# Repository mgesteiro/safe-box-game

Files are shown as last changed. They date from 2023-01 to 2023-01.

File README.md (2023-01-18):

# Safe BOX GAME puzzle-box

This is a **funny puzzle-box** game in which you have to try to guess -using the lights- the correct four digit code to open the safe box.

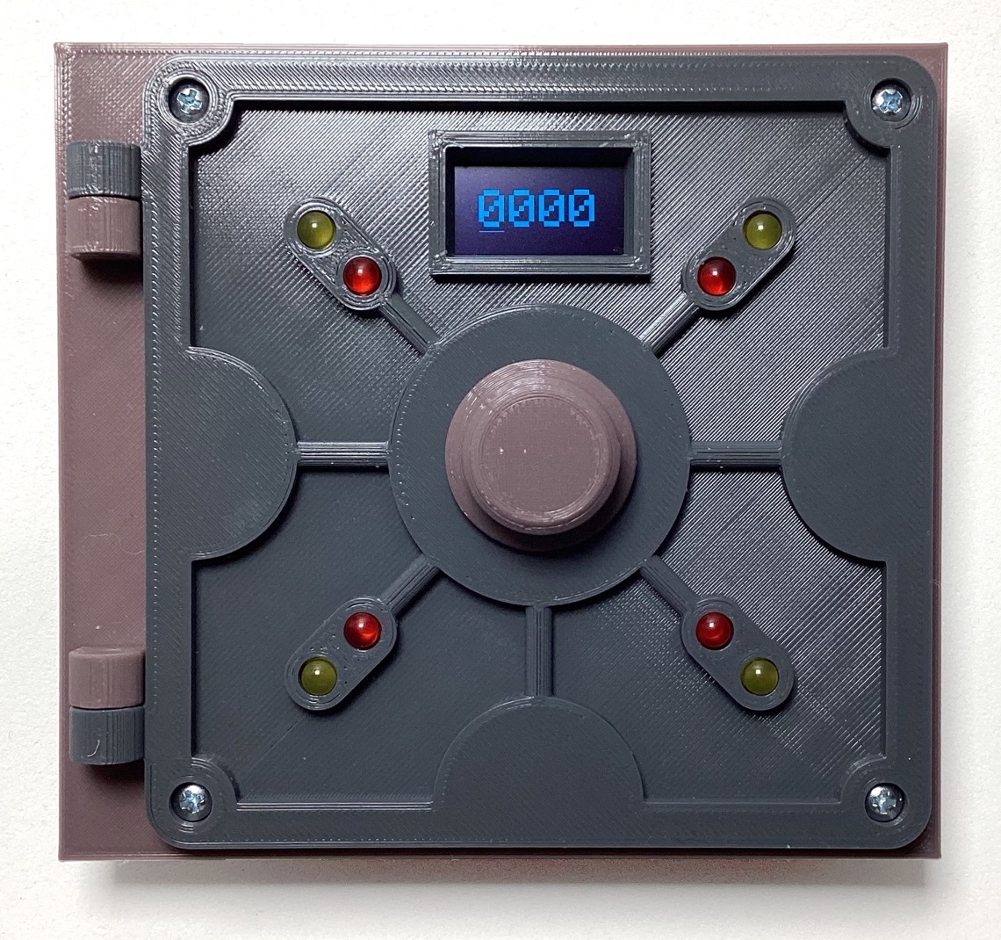
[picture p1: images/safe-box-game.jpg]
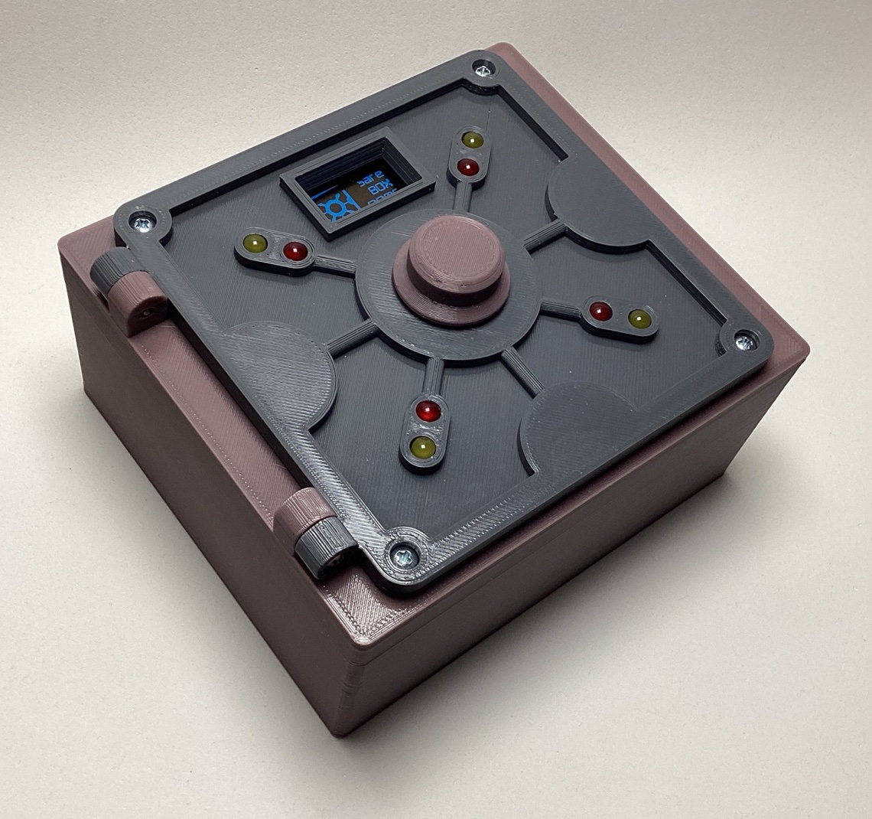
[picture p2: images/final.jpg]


This puzzle-box game was inspired by and based on [this project](https://www.the-diy-life.com/crack-the-code-game-built-into-a-diy-safe-puzzle-box/), making it **more compact** (it's all self-contained now), **3D printed** (instead of laser cut) and **rechargable**.

Any sugestion? Please, **contact me**.

## USAGE

The box is unlocked when it's off, so you can open the door if you want. These are the steps:

* Turn-on the system pressing the switch in the back of the door (inside the box when closed): you'll see a welcome screen.
* After that, a message appears asking you to press the knob to lock the door: close the door and press it.
* Now you have a four digit code in the screen: rotate the know to change the number, and press it to go to the next digit.
* When you press the knob in the last digit, the safe checks the combination: if it is right, the door will unlock and you'll have won; if not, it will tell you so and the *lights* will indicate how many digits were correct and how many were in the correct position.
* Repeat until you get it!

**NOTE:** there is a blinking light (every two seconds) that has NO meaning. It's just an *I'm alive* signal.

## WHY and HOW

The original project was **very very** appealing, but had **two big drawbacks** for me:

* I don't have a laser cutter (but yes a 3D-printer), and
* The control and electronic components were **too spread** (part in the door, part in the back).

Based on my experience in previous projects, I was convinced that it could be done in a much more compact form, using also a rechargable system and improving a little bit the UX (that was excellent to begin with).

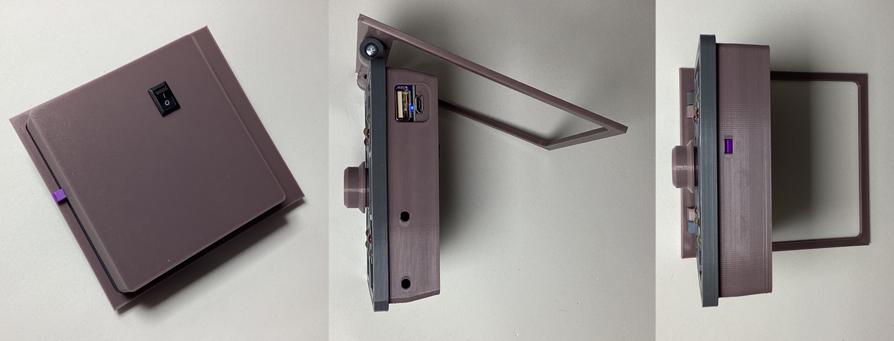
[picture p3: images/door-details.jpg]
door-details

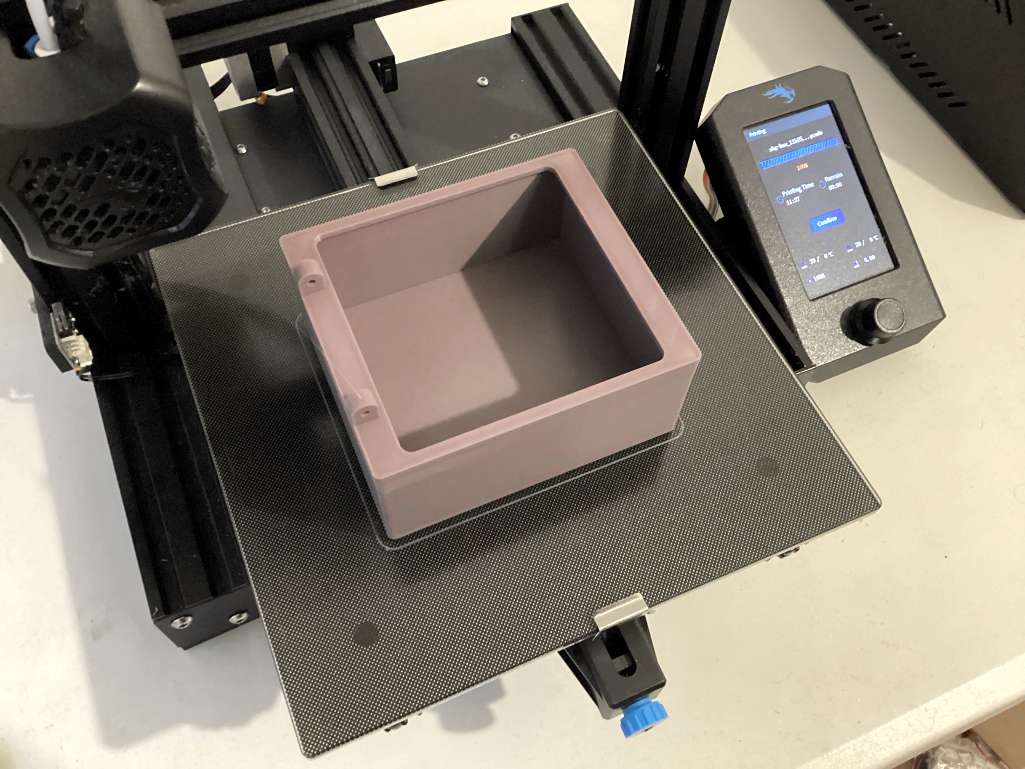
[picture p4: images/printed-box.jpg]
printed-box


And here it is the result, after a little bit more effort than I anticipated... 😅

## 3D

All the **3D parts** (available in the [`3D`](3D) folder) were created using the open-source and free software [FreeCAD](https://www.freecad.org). If you want, for example, a bigger box, go ahead and edit the 3D file to do so. In the [`STLs`](3D/STLs) subfolder reside all the STL files ready to be 3D printed, with **no supports** required at all: it's a very easy print.

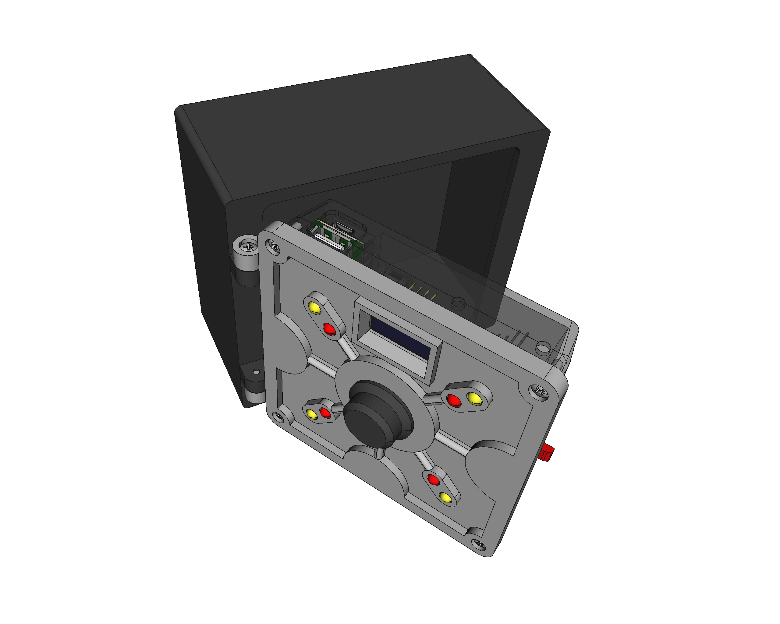
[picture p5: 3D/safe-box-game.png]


There were some interesting **design challenges**, like how to make all the parts ***no-support-required*** 3D-printable, that led to interesting choices that I wouldn't have done other way: the (***good looking***) screws holding the door together are accesible from the outside, and, from a *security perspective*, that would've been disastrous... if this was a *real* safe-box. It actually became a ***handy feature***: if anything anomalous/unexpected happens (battery depletion?) and you can't open the box, you have always the option to disassemble it unscrewing those four screws 👌

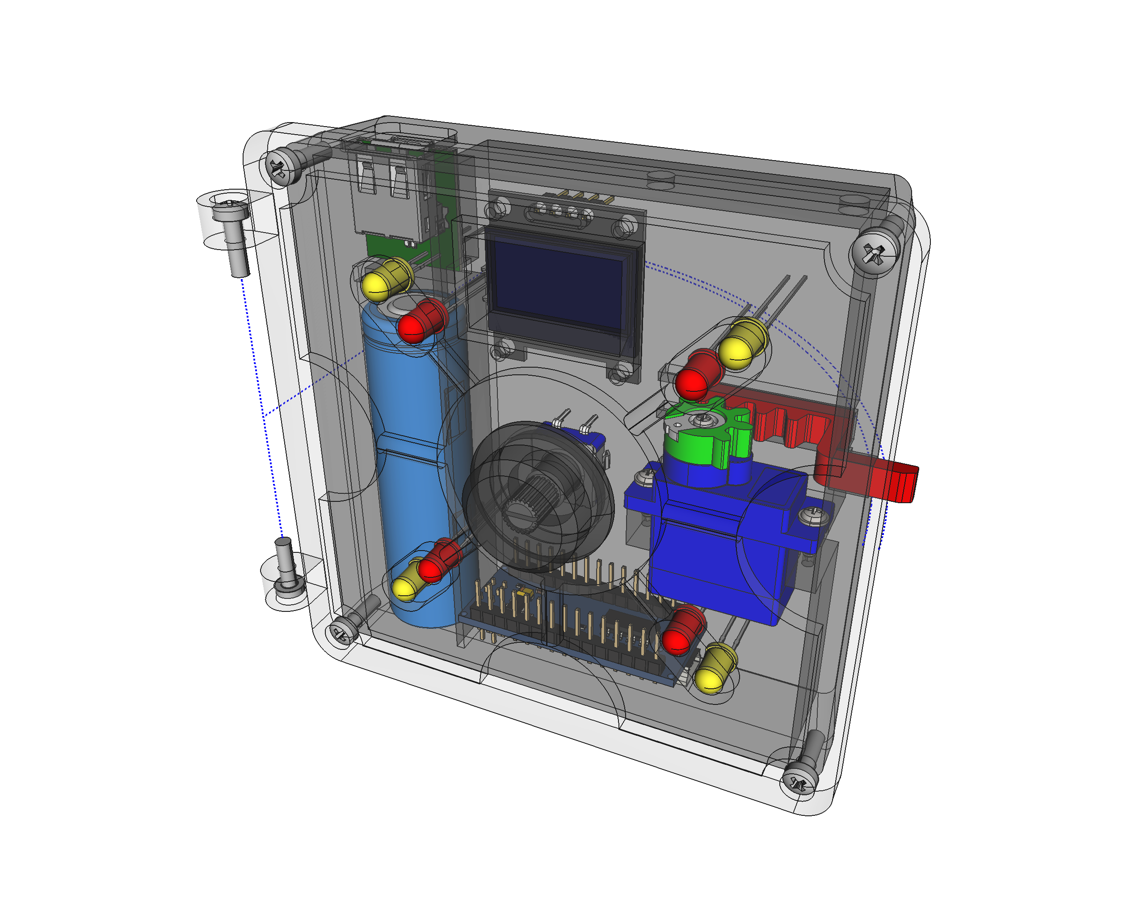
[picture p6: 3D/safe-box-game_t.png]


Did you notice the blue dashed lines? Yep, they were added after realizing that the door was going to be **THICK** and that I needed to change the design to provide rotation clearance without making it even bigger or make a too lousy frame (compact, remember?). After some back and forth between the door, the hinges and the frame, everything  ended up really well. 

This is also the first time I've worked with [*gears & racks*](3D/servo-gearandrack), but was a nice opportunity to make the locking mechanism much more nicer than just a *big rotating contraption*, and contributed to make everything more compact. I had also to \[re\]create some parts, like the [SDD1306 oled display](https://github.com/mgesteiro/FreeCAD-models/tree/master/SSD1306_128x64), because the available models didn't match what I had at hand.

At the end, the door looks like a *real* safe-box door, with all its thickness and shape and weight ... **I ❤️ it!**.

## CONNECTIONS

This is the schematic of the system, created using the open-source software [Fritzing](https://fritzing.org) and available in the [`connections`](connections) folder.

connections

In the original project, the servo was connected directly to the Arduino 5V output, which is generally not recommended (even for the small SG90 micro-servo**). As I opted to power everything with a 5V powerbank-DIY kit, the servo can be powered directly (althoug a capacitor in parallel is always a good idea...), making the whole device also **rechargable**.

** as it may demand quite a lot of current that the Arduino may not be able to provide and get *swamped* in the process, resetting itself.

In the physical world it was a little more difficult than I wanted, but with patience, care and some *creativity* and *dexterity*, it ended up nicely:

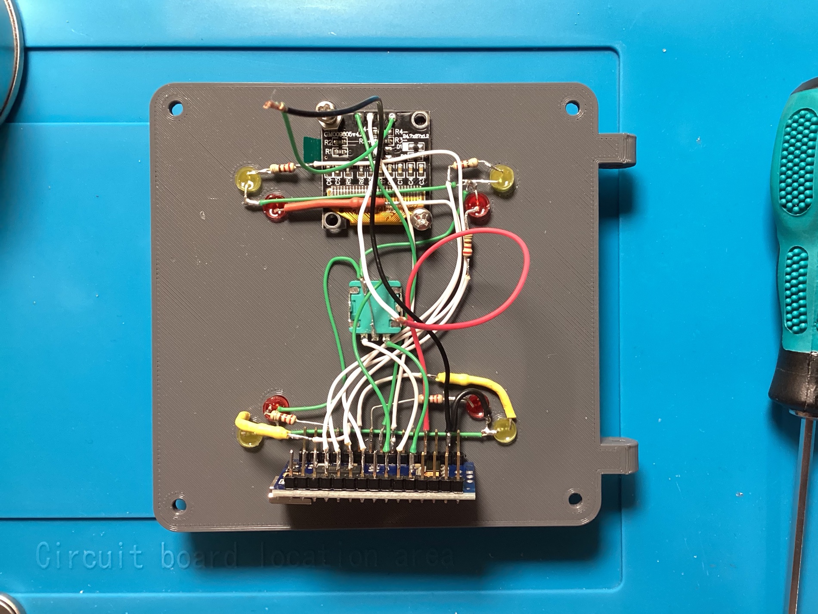
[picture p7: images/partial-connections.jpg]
partial-connections


The most difficult part were the LEDs to the right, that had to go flat because they are under the rechargable system with very little space. The servo also played an important role in *limiting* the available space. The [3D model](#3d) was very useful to navigate all these problems beforehand and during the assembly.

## CODE

The puzzle-box is powered by an **Arduino Nano** which can be programmed with the [Arduino IDE](https://www.arduino.cc/en/software). The code itself is available in the [`code/sbg`](code/sbg) folder:

* It solves a bug in the original project's code, where there were no **9**'s in the digits, due to an incorrect use of the [`random()`](https://www.arduino.cc/reference/en/language/functions/random-numbers/random/) function.
* Nice cursor to indicate which digit is being manipulated.
* It comes with and *adhoc* library (***RotEnLib***) to manage the rotary encoder (with momentary push button) and make the code simpler while having nice features like *debouncing* and *round-robin* hidden away.
* It has some configuration parameters at the beginning (`sbg.ino`) that can be adjusted to your needs.
* There is some code to avoid the powerbank auto-shuting-down function (that's why the LEDs blink!).
* And a nice *splash screen* (see [`code/logo`](code/logo)).



## REFERENCES

* Crack-the-Box project by Michael Klemets from the The DIY Life: [www.the-diy-life.com/crack-the-code-game-built-into-a-diy-safe-puzzle-box/](https://www.the-diy-life.com/crack-the-code-game-built-into-a-diy-safe-puzzle-box/)
* Arduino `random()` function: [www.arduino.cc/reference/en/language/functions/random-numbers/random/](https://www.arduino.cc/reference/en/language/functions/random-numbers/random/)
* My FreeCAD 3D models repository: [github.com/mgesteiro/FreeCAD-models](https://github.com/mgesteiro/FreeCAD-models)
* My Fritzing parts repository: [github.com/mgesteiro/fritzing-parts](https://github.com/mgesteiro/fritzing-parts)
* **FreeCAD** 3D CAD modelling software: [www.freecad.org](https://www.freecad.org)
* **Fritzing** schematics and PCB modelling software: [fritzing.org](https://fritzing.org)

## LICENSE

This work is licensed under the [GNU General Public License v3.0](LICENSE-GPLV30). All media and data files that are not source code are licensed under the [Creative Commons Attribution 4.0 BY-SA license](LICENSE-CCBYSA40).

More information about licenses in [Opensource licenses](https://opensource.org/licenses/) and [Creative Commons licenses](https://creativecommons.org/licenses/).

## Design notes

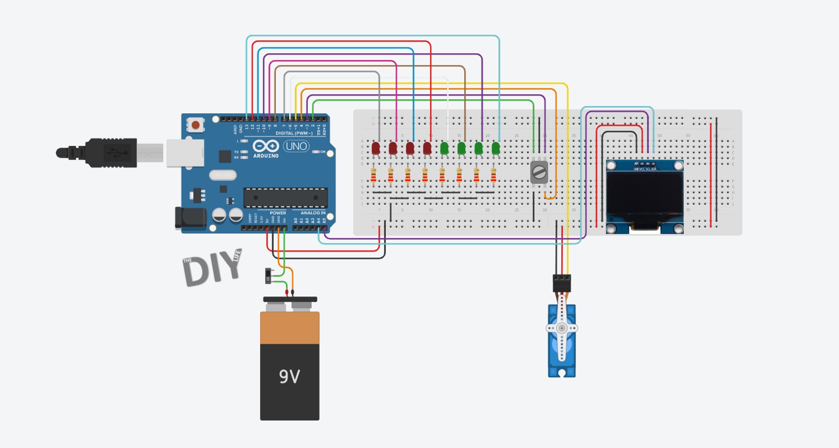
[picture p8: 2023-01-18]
docs/Crack-The-Code-Schematic.jpg

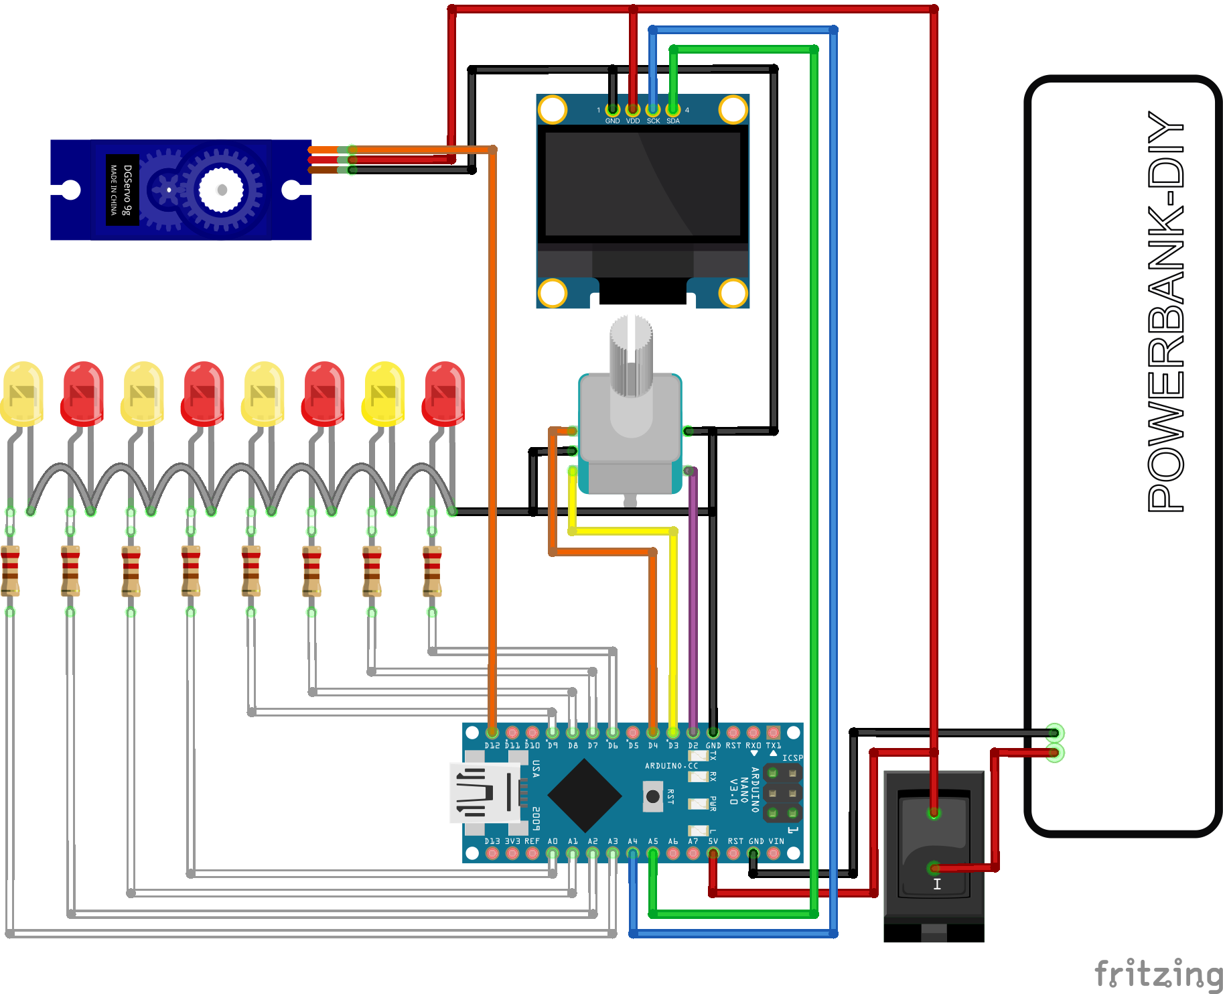
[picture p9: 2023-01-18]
connections/connections_bb.png

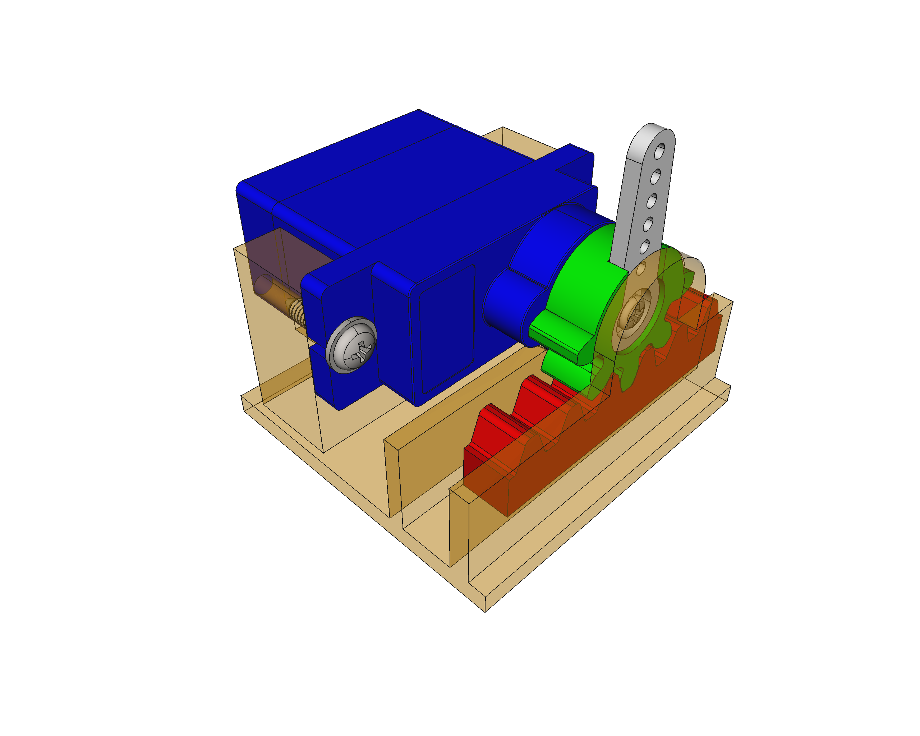
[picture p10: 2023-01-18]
3D/servo-gearandrack/servo-gearandrack.png

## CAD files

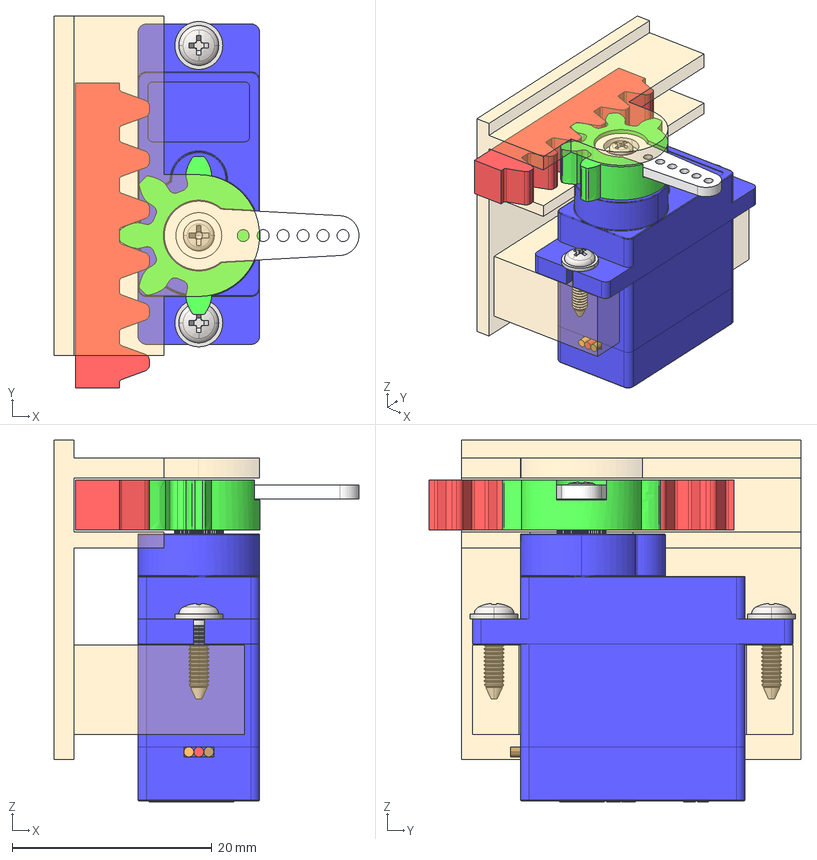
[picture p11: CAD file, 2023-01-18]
3D/servo-gearandrack/servo-gearandrack.FCStd
30.6 x 37.3 x 36.2 mm
Body-gear
Body-rack
Body-servo-support
arm1
screw-shaft
screw1
screw2
body-screws x 2
w1 x 2
shaft x 2
w3 x 2
w2 x 2

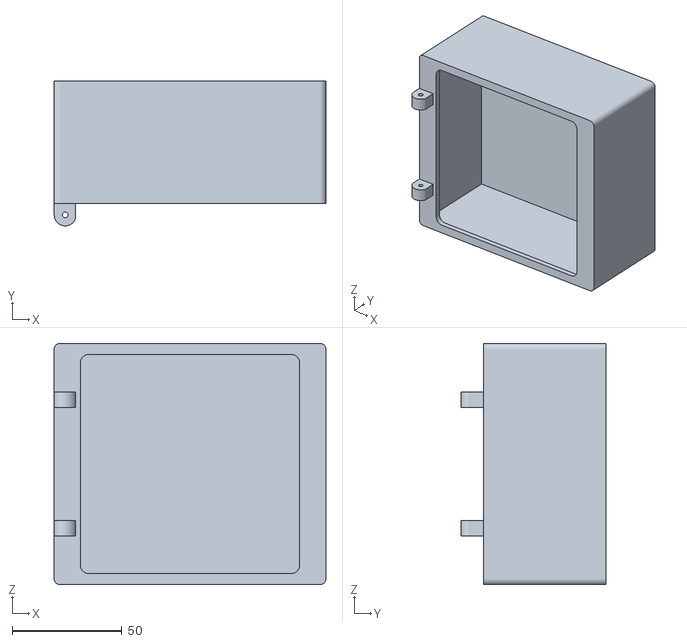
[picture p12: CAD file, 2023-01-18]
3D/STLs/sbg-box.stl
124.0 x 66.0 x 110.0

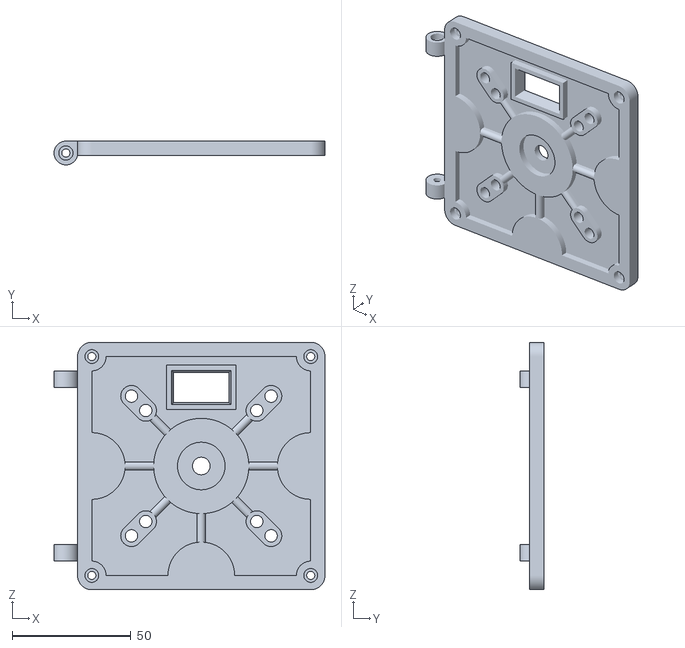
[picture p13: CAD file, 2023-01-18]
3D/STLs/sbg-door.stl
113.9 x 10.00 x 104.0

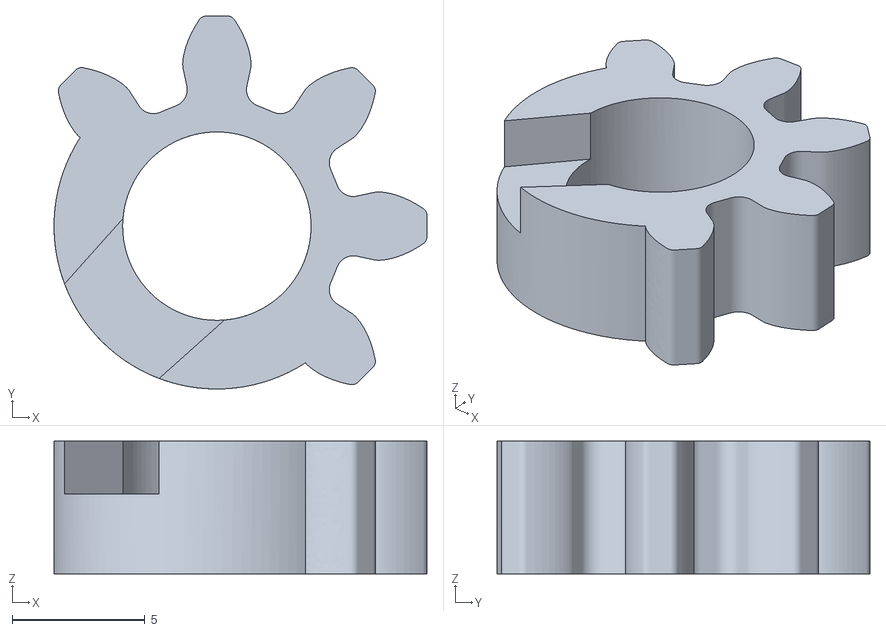
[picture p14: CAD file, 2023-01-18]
3D/STLs/sbg-gear.stl
14.1 x 14.1 x 5.00

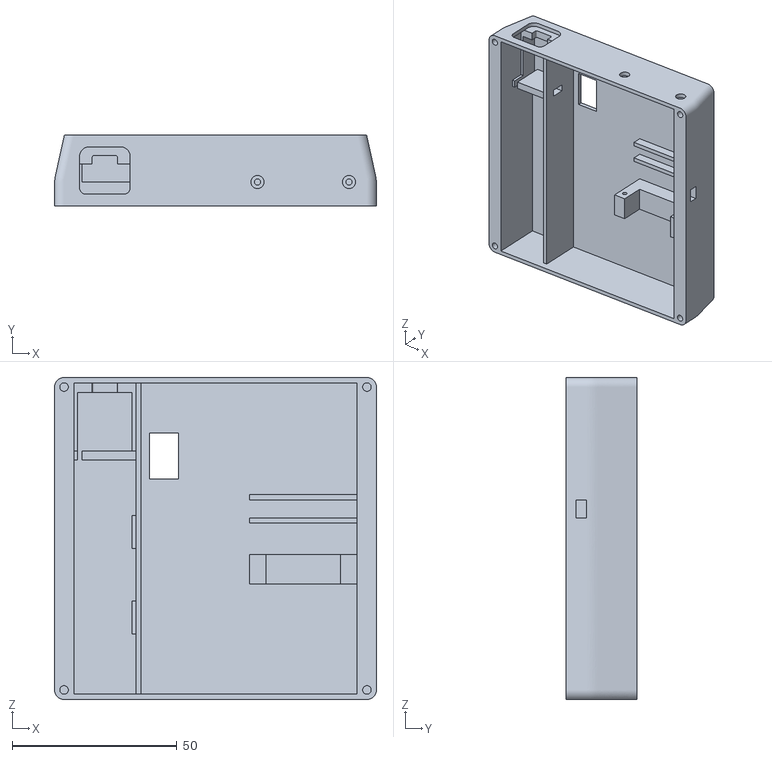
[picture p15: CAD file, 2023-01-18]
3D/STLs/sbg-electronic-box.stl
97.8 x 21.6 x 97.8

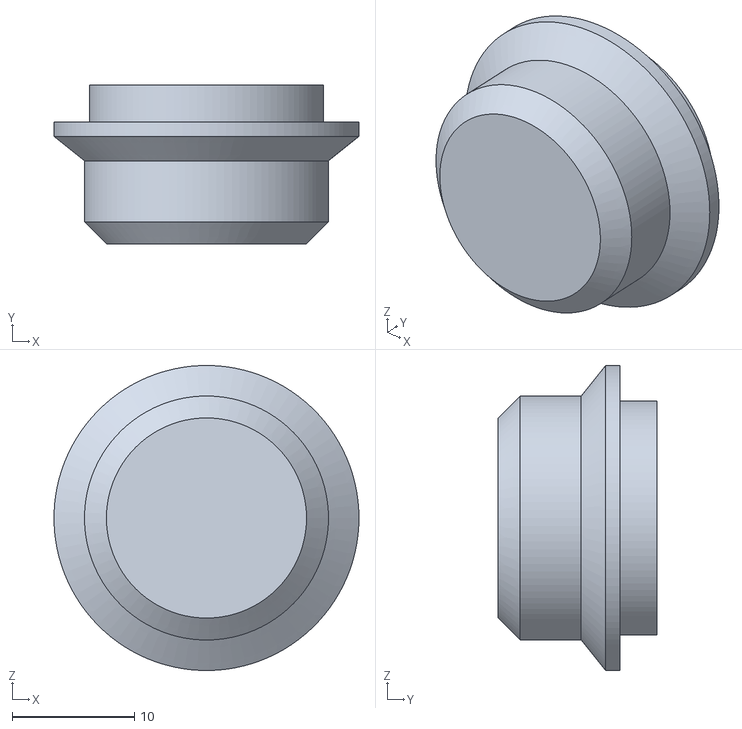
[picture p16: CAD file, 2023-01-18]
3D/STLs/sbg-knob.stl
25.0 x 13.0 x 25.0

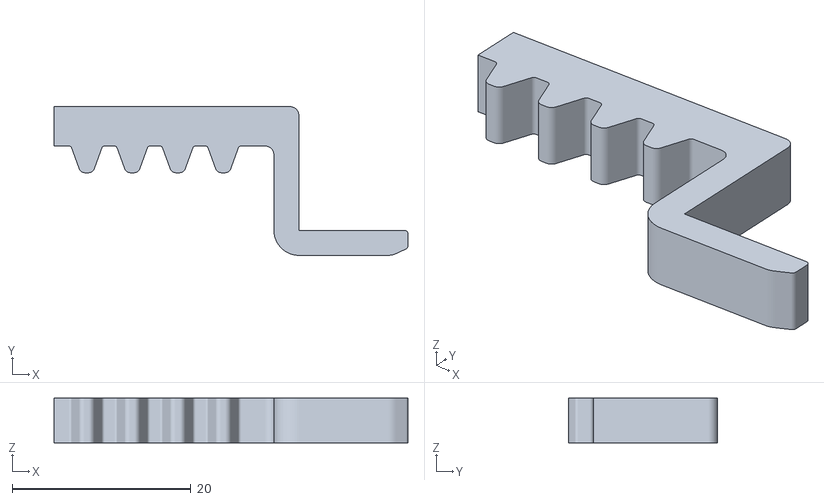
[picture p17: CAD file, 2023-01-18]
3D/STLs/sbg-rack-lock.stl
39.6 x 16.6 x 5.00

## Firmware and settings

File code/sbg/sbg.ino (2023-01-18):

/**
 * Safe BOX GAME firmware.
 *
 * @author mgesteiro
 * @version 1.0.0
 * @date 20230115
 * @copyright OpenSource, LICENSE GPLv3 and CCSABY40
 *
 * Libraries required: "Servo" and "Adafruit_SSD1306" (and dependencies)
 */

#define VERSION "1.0.0"

// CONFIGURATION
#define REL_PINA 2
#define REL_PINB 3
#define REL_BTN 5
#define SCREEN_ADDRESS 0x3C
#define SERVO_PIN 12
#define SERVO_UNLOCKED 110
#define SERVO_LOCKED 55
#define SHOW_RESULTS_IN_SCREEN false

#include "RotEnLib.h"  // rotary encoder library
#include <Adafruit_SSD1306.h>
#include "SBGlogo.h"  // startup screen
#include <Servo.h>

RELEncoder encoder = RELEncoder(REL_PINA, REL_PINB, REL_BTN, 0, 9, true); // pinA, pinB, btn, min, max, circular
Adafruit_SSD1306 display(128, 64, &Wire, -1);
Servo lockServo;

const uint8_t correctPositionPins[] = {7, 8, A2, A1};
const uint8_t correctNumberPins[]   = {6, 9, A3, A0};
uint8_t code[4], guess[4];
uint8_t currentDigit = 0;

uint32_t tactivity = 0;
uint8_t LEDstate = 0;

/**
 *******************************************************************************
 *   S E T U P   &   L O O P
 */

void setup()
{
  Serial.begin(9600);
  Serial.print("Safe BOX GAME v");
  Serial.println(VERSION);
  // LEDs
  initLEDs();
  // Encoder button callback
  encoder.setButtonOnPressCB(onButtonPressed);
  encoder.init();
  // Display
  if (!display.begin(SSD1306_SWITCHCAPVCC, SCREEN_ADDRESS))
    Serial.println(F("SSD1306 allocation failed"));
  display.setTextColor(SSD1306_WHITE);
  // Servo
  lockServo.attach(SERVO_PIN);
  lockServo.write(SERVO_UNLOCKED);  // unlock the safe
  // Seed PRNG
  randomSeed(analogRead(A7));  // noise from A7 (not connected = floating)
  // Do intro
  doSplash();
  introLEDs();
  // Do start
  doStart();
}  // setup()

void loop()
{
  // avoids power-bank shutting down
  checkStandBy();

  // update encoder status
  encoder.loop();

  // get encoder position
  uint8_t position = encoder.getPosition();

  // redraw output if necessary
  if (position != guess[currentDigit])
  {
    guess[currentDigit] = position;
    updateDisplay(guess, currentDigit);
  }

  // the rest of the logic is done at the
  // encoder's onButtonPressed() callback
  // function where the "clicks" are processed

}  // loop()


/**
 *******************************************************************************
 *   S U P P O R T   F U N C T I O N S
 */

 void initLEDs()
{
  for (uint8_t i = 0; i < 4; i ++)
  {
    pinMode(correctPositionPins[i], OUTPUT);
    pinMode(correctNumberPins[i], OUTPUT);
  }
}

/**
 * Turn on/off each LED individually in bulk.
 *
 * @param state 1 bit per LED. Low nibble for "correct position" LEDs and
 *              high nibble for "correct number" LEDs.
 */
void turnLEDs(uint8_t state)
{
  LEDstate = state;  // save for standby check
  for (uint8_t i = 0; i < 4; i ++) digitalWrite(correctPositionPins[i], bitRead(state, i));
  for (uint8_t i = 4; i < 8; i ++) digitalWrite(correctNumberPins[i-4], bitRead(state, i));
}

/**
 * Show splash screen
 */
void doSplash()
{
  display.clearDisplay();
  display.drawBitmap(0, 0, logo_data, 128, 64, 1);  // put logo
  display.display();  // show logo
  delay(1000);
}

/**
 * LEDs animation.
 */
void introLEDs()
{
  // nice crack the code original animation
  uint8_t Anim[][2] =
  {
    {B00001111, 30},  // state, delay (in 10ms chunks)
    {B11110000, 30},
    {B00001111, 30},
    {B11110000, 30},
    {B11111111, 130},
  };
  for (uint8_t i = 0; i < sizeof(Anim)/2; i ++)
  {
    turnLEDs(Anim[i][0]);
    delay(Anim[i][1]*10);
  }
  turnLEDs(0);
}  // introLEDs()

/**
 * Generate a new code and clear current guess.
 */
void doCodes(bool show)
{
  for (uint8_t i = 0; i < 4; i ++)
  {
    code[i] = random(0,10);  // values from 0 to 9
    guess[i] = 0;
  } 
  // show code
  if (!show) return;
  Serial.print("New code: ");
  for (uint8_t i = 0; i < 4; i ++) Serial.print(code[i]);
  Serial.println();
}  // doCodes()

/**
 * Cycles through the "open", "wait for click", and "closed" states for
 * the lock. This is done this way because it is always what happens:
 * during the start and after a win.
 */
void doLock()
{
  // first: unlock and show message to lock
  lockServo.write(SERVO_UNLOCKED);  // unlock the safe
  display.clearDisplay();
  //display.invertDisplay(true);
  display.setTextSize(1);
  display.setCursor(30,18);
  display.print(F("pulsa para"));
  display.setTextSize(2);
  display.setCursor(30,30); 
  display.print(F("CERRAR"));
  display.display();
  // second: wait for user input
  waitForClick(0);
  // finally: lock and show the notification for 2 secs.
  lockServo.write(SERVO_LOCKED);  // lock the safe  
  display.clearDisplay();
  display.setTextSize(2);
  display.setCursor(23,25);
  display.print(F("CERRADO"));
  display.display();
  delay(2000);
  //display.invertDisplay(false);
}  // doLock()

/**
 * Shows current guess-code and a cursor under the current digit being manipulated.
 *
 * @param guess guess code introduced by the user
 * @param digitpos position of the digit currently being updated
 */
void updateDisplay(uint8_t guess[], uint8_t digitpos)
{
  String text = "";
  for (uint8_t i = 0; i < 4; i++) text += guess[i];  // code[] to String
  display.setTextSize(4);
  display.clearDisplay();
  // default font size 5x7 (pixels) + 1 pixel separation between characters
  // (SCREEN_WIDTH - CHARACTER_WIDTH * PIXEL_MULTIPLIER * NUMBER_OF_DIGITS - (NUMBER_OF_DIGITS - 1) * PIXEL_MULTIPLIER) / 2
  // (128 - 5 * 4 * 4 - (4 - 1) * 4 ) / 2 = 18 <-- X
  // (SCREEN_HEIGHT - CHARACTER_HEIGHT * PIXEL_MULTIPLIER) / 2
  // ( 64 - 7 * 4 ) / 2 = 18 <-- Y
  display.setCursor(18, 16);  // 16 instead of 18 -> some room for under-cursor
  display.println(text);
  display.drawRect(18 + (digitpos * 24), 47, 20, 3, SSD1306_WHITE);  // under-cursor
  display.display();   
}  // updateDisplay()

/**
 * Shows the valid positions/numbers in the screen.
 *
 * @param validpos number of digits in valid position
 * @param validnum number of valid digits
 */
void showCheckResults(uint8_t validpos, uint8_t validnum)
{ 
  // LEDs
  // lo - positions, hi - numbers
  uint8_t state = B00000000;
  uint8_t mask = B00000001;
  for (uint8_t i = 0; i < validpos; i ++)
  {
    state |= mask;
    mask <<= 1;
  }
  mask = B00010000;
  for (uint8_t i = 0; i < validnum; i ++)
  {
    state |= mask;
    mask <<= 1;
  }
  turnLEDs(state);
  // Display
  display.clearDisplay();
  display.setTextSize(2);
  #if SHOW_RESULTS_IN_SCREEN
  // (128 - 6 * 5 * 2 - 5 * 2 ) / 2 = 29
  // (64 - 2 * 7 * 2 - 1 * 2 ) / 2  = 17
  String text = "NUM: ";
  text += validnum;
  display.setCursor(29, 17);
  display.print(text);
  text = "POS: ";
  text += validpos;
  display.setCursor(29, 33);
  display.print(text);
  #else
  display.setCursor(5, 25);
  display.print("INCORRECTO");
  #endif
  display.display();
}  // showCheckResults()

/**
 * Initialization routine: new code and reset parameters.
 */
void doStart()
{
  doLock();  // unlock, wait for click, lock
  doCodes(true);  // generate new code, clear guess
  currentDigit = 0;  // reset
  encoder.setPosition(guess[currentDigit]);  // reset
  updateDisplay(guess, currentDigit);  // show initial status
}

void doWin()
{
  display.clearDisplay();
  display.setTextSize(2);
  display.setCursor(5, 25);
  display.print("CONSEGUIDO");
  display.display();
  lockServo.write(SERVO_UNLOCKED); // before intro
  introLEDs();
}

/**
 * Callback function to attend the encoder "OnPressed" event
 *
 * @param encoder which encoder sends the event
 * @param when moment in which occurred
 */
void onButtonPressed(RELEncoder& encoder, unsigned long when)
{
  currentDigit ++;  // change to next digit
  if (currentDigit > 3)  // was it the last digit?
  {
    // check provided code
    uint8_t copy[4]; // local copy of code for manipulation
    memcpy(copy, code, 4);
    // checking positions/numbers
    uint8_t validpos = 0, validnum = 0;
    for (uint8_t i = 0; i < 4; i++)
    {
      // valid position
      if (guess[i] == code[i]) validpos ++;
      // valid number
      for (uint8_t j = 0; j < 4; j++)
        if (guess[i] == copy[j]) {
          validnum ++;
          copy[j] = -1; // mark as used
          break; // no more checking
        }
    }
    // checking victory
    if (validpos == 4)
    {
      doWin();  // shows message
      doSplash();  // splash screen
      waitForClick(0);  // user must click
      doStart(); // start-up procedure
      return;
    }
    // show checking results
    showCheckResults(validpos, validnum);
    waitForClick(2000);  // 2 secs. maximum
    turnLEDs(0);
    // go to the beginning
    currentDigit = 0;
  }
  // update
  encoder.setPosition(guess[currentDigit]);
  updateDisplay(guess, currentDigit);

} // onButtonPressed()

/**
 * Checks that there is at least a minimum power consumption,
 * to avoid the power-bank shutting off.
 */
void checkStandBy()
{
  uint32_t tnow = millis();
  if (tnow - tactivity > 2000)
  {
    if (! LEDstate)
    {
      turnLEDs(B01000100 << random(0,2)  );  // turn-on a random pair of LEDs
      delay(5);  // for 5 milliseconds
      turnLEDs(0);
      tactivity = tnow; 
    }
  }
}

/**
 * Waits until the user clicks or the provided milliseconds pass.
 *
 * @param delay max time to wait, in milliseconds. Infinite if value is 0.
 */
void waitForClick(uint32_t tdelay)
{
  if (tdelay == 0) tdelay = 0xffffffff;
  delay(150);  // give time for button to be released
  uint32_t tnow = millis();
  while ( 
    (digitalRead(REL_BTN) == HIGH)
    && (millis() - tnow < tdelay)
  ) checkStandBy();
}

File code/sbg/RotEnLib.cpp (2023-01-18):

// RotEnLib
// --------
// author: mgesteiro
// date: 20211205

#include "RotEnLib.h"
#include "Arduino.h"

#define BTNDEBOUNCETIME 10
#define ENCDEBOUNCETIME 4
#define LONGPRESSTIME 800

// constructor
RELEncoder::RELEncoder(int S1, int S2, int btn, int min, int max, bool circular=false, int threshold=15, int thdelta=10)
{
  // Remember Hardware Setup
  _s1 = S1;
  _s2 = S2;
  _btn = btn;
  _min = min;
  _max = max;
  _circ = circular;
  _th = threshold;
  _thd = thdelta;
  
  // initial state
  _position = 0;
  _s1State = 0;
  _s1LastState = 0;
  _btnState = HIGH;
  _btnLastState = HIGH;
  _btndebouncing = false;
} // RELEncoder()

void RELEncoder::init()
{
  // Setup the input pins and turn on pullup resistor
  pinMode(_s1, INPUT_PULLUP);
  pinMode(_s2, INPUT_PULLUP);
  pinMode(_btn, INPUT_PULLUP);
}

int RELEncoder::getPosition()
{
  return _position;
} // getPosition()

void RELEncoder::setPosition(int newpos)
{
  _position = newpos;
} // setPosition()

int RELEncoder::getBtnState()
{
  return _btnState;
} // getBtnState()

void RELEncoder::setButtonOnPressCB(ButtonEventCallback callback)
{
  _callbackOnPress = callback;
} // setButtonOnPressCB()

void RELEncoder::setButtonOnReleaseCB(ButtonEventCallback callback)
{
  _callbackOnRelease = callback;
} // setButtonOnReleaseCB()

void RELEncoder::setButtonOnLongPressCB(ButtonEventCallback callback)
{
  _callbackOnLongPress = callback;
} // setButtonOnReleaseCB()

void RELEncoder::loop(void)
{
  unsigned long nowt = millis();
  // BUTTON
  int btnState = digitalRead(_btn);
  if (
      (btnState != _btnState) // button changed state
      && (! _btndebouncing) // not counting time yet
     ) 
  {
    // start counting (debounce time)
    _btnsavedt = nowt;
    _btndebouncing = true;
  }
  if (
      (_btndebouncing) // counting time 
      && ((nowt - _btnsavedt) > BTNDEBOUNCETIME) // bigger than debounce time
     ) 
  {
    // change of state
    if (_btnLastState != _btnState) _btnLastState = _btnState;
    _btnState = btnState;
    _btndebouncing = false;
    if ((_btnLastState == LOW) && (_btnState == HIGH)) if (_callbackOnRelease) _callbackOnRelease(*this, nowt-_btnpressed);
    if ((_btnLastState == HIGH) && (_btnState == LOW))
    {
      _btnpressed = nowt;
      if (_callbackOnPress) _callbackOnPress(*this, _btnpressed);
    }
  }
  if ((_btnLastState == HIGH) && (_btnState == LOW) && ((nowt-_btnpressed)>LONGPRESSTIME)) {
    //_btnLastState == LOW; //stop
    if (_callbackOnLongPress) _callbackOnLongPress(*this, nowt-_btnpressed);
    _btnpressed=nowt;
  }
  
  // ENCODER
  _s1State = digitalRead(_s1);
  // check if S1 has changed -> that means a pulse has occured
  if (_s1State != _s1LastState) {
    // simple debouncing filter
    if ((nowt-_encsavedt) < ENCDEBOUNCETIME) return;
    // only count when S1 is LOW
    if (! _s1State) {
      int delta = ((nowt-_encsavedt) < _th) ? _thd : 1;
      // if S2 state is the same as S1 state -> the encoder is rotating clockwise
      if (digitalRead(_s2) == _s1State) _position+=delta;
      else _position-=delta;

      if (_position > _max) _position = (_circ ? _min : _max);
      if (_position < _min) _position = (_circ ? _max : _min);

      _encsavedt=nowt; 
    }
  } 
  _s1LastState = _s1State;
} // loop()

// end
